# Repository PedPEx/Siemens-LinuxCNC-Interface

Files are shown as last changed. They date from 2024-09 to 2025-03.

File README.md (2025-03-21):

# Siemens Sinumerik840C control panel Interface (WIP! - UNTESTED!)
This interface board is designed to be placed on the backside of an [old type](https://mall.industry.siemens.com/mall/de/de/Catalog/Product/6FC5103-0AD03-0AA0) Siemens Sinumerik840C machine control panel in order to be used as user input in LinuxCNC. I reverse engineered a control panel of type M (CNC-Mill - 6FC5103-0AD03-0AA0) for this project. All the IOs of these control panels are accessible through the two 64pin pinheaders. You can get these machine control panels pretty cheap on ebay.

Interface:
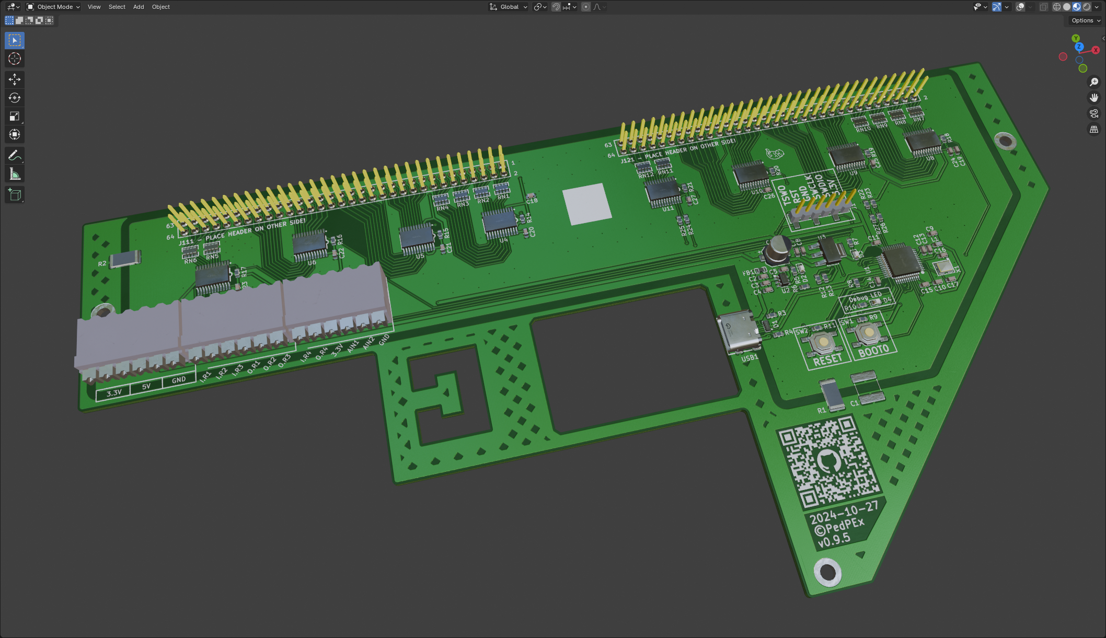
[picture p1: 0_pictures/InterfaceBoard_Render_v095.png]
v0.9.5 Blender render v0.9.5


Sinumerik840C Machine Control Panel:
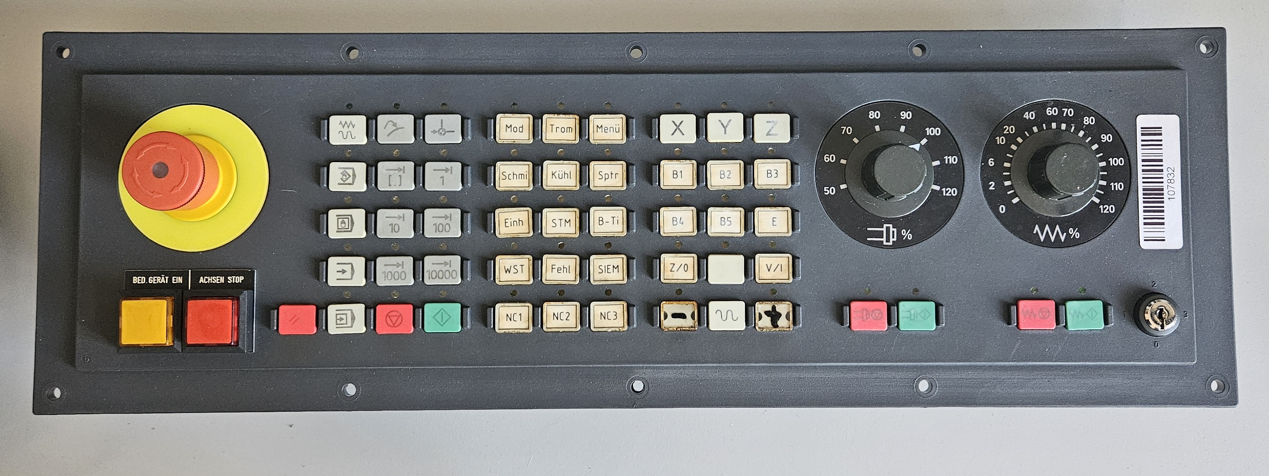
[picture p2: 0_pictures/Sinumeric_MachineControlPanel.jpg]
Sinumerik840C Machine Control Panel


## ToDo
- ✅ finished prototype PCB (v0.9.5)
- 🔲 finished prototype PCB (v0.9.6)
- ✅ firmware for STM32L151CC (technically 100% - needs cleanup and timeout detection on LinuxCNC side)
- 🔲 tested intensively with LinuxCNC
- 🔲 example config for LinuxCNC

## Powering
The board needs no seperate supply voltage and is fully powered by the USB Interface. A power distribution switch deactivates the whole interface in case of an overcurrent (set to 1.0 A).

## USB port
Plug in a USB-C cable and use the provided strain relief with the help of a 5mm cable tie. With this USB connection a virtual serial port is used to send the data to the host. More information in the [software](#usagesoftware) details.

## Terminal blocks and general IO
Most of the IO on the three terminal blocks is directly wired into the microcontroller. They can be used for analog inputs or for further expansion in general.

As terminal blocks [Weidmüller 1824460000 - LSF-SMT 3.50/06/90 3.5SN BK TU](https://catalog.weidmueller.com/catalog/Start.do?ObjectID=1824460000) were used - because i had them at hand. But any headers or screw terminals with a 3.5 mm pitch can be used here.

## Usage/Software
This interface board is meant to be used in combination with the software [LinuxCNC_ArduinoConnector](https://github.com/AlexmagToast/LinuxCNC_ArduinoConnector). It does not operate with an Arduino, but with a much more capable [STM32L151C8](https://www.st.com/en/microcontrollers-microprocessors/stm32l151cc.html). The STM32 just emulates a serial port and sends the same signals to the LinuxCNC component like the Arduino would. The L1 series of STM32 was chosen because of its bootloader

## Limitations
Do not use this board for any time critical porpuses!

## Online Preview / BOM
[Detailed schematics preview](https://kicanvas.org/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) (KiCanvas)

[Online BOM](https://htmlpreview.github.io/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)

[3D Preview](https://github.com/PedPEx/Siemens-LinuxCNC-Interface/blob/master/1_hardware/Siemens-Sinumerik840C-Maschinensteuertafel-Adaptor.stl)

## LinuxCNC config (TODO)
When finished, an example config for LinuxCNC can be found in the [correspondig folder](https://github.com/PedPEx/Siemens-LinuxCNC-Interface/tree/master/2_software_LinuxCNC).

An example of a whole machine fitted with this Interface can be found in my other project [Maho400E-LinuxCNC](https://github.com/PedPEx/Maho400E-LinuxCNC)

## *Note*
The pictures were rendered with the help of Blender and the [pcb2blender](https://github.com/30350n/pcb2blender) plugin and the HTML BOM was created with [InteractiveHtmlBom](https://github.com/openscopeproject/InteractiveHtmlBom).

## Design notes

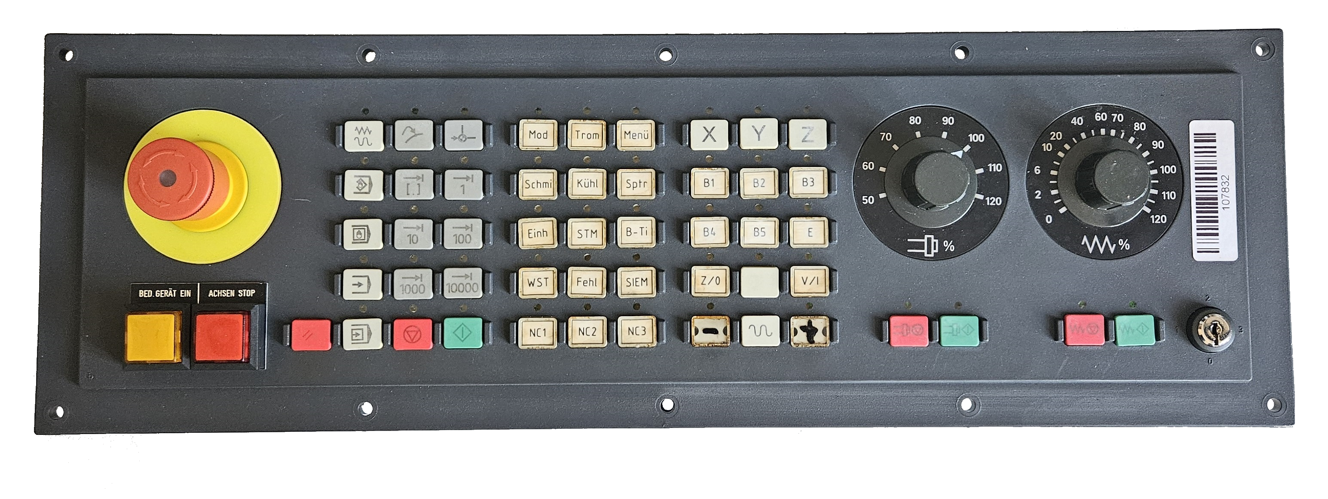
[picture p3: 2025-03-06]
0_pictures/Sinumeric_MachineControlPanel.png

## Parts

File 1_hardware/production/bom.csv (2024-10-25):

Designator | Footprint | Quantity | Value | LCSC Part #
C1 | 2220 | 1 | 0.1u | C5290327
C10, C11, C13, C14, C15, C19, C20, C21, C22, C24, C25, C26, C27 | 0603 | 13 | 100n
C12, C2 | 0603 | 2 | 1u
C16, C17 | 0603 | 2 | 8p
C18, C23, C9 | 0603 | 3 | 4u7
C3, C8 | 0603 | 2 | 10u
C4, C5, C7 | 0603 | 3 | 0.1u
C6 | CP_Elec_5x5.8 | 1 | 100u | C336771
D1 | USON-10_L2.5-W1.0-P0.50-BL | 1 | TPD4E05U06DQAR_C138714 | C138714
D2, D3, D4 | 0603 | 3 | LED
FB1 | L0603 | 1 | 100R@100MHz | C107332
J1 | HDR-SMD_6P-P2.54-V-M-LS4.8_R2 | 1 | ProgHeader | C2883763
J111, J121 | SAMTEC_SSW-132-24-L-D | 2 | SSW-132-24-L-D
J2 | 1824460000 - LSF-SMT 3.500690 3.5SN BK TU | 1 | Power
J3 | 1824460000 - LSF-SMT 3.500690 3.5SN BK TU | 1 | Buttons
J4 | 1824460000 - LSF-SMT 3.500690 3.5SN BK TU | 1 | Reserve2
L1 | 0603 | 1 | 27nH | C12100
R1, R2 | 2512 | 2 | 100k | C25717
R10, R7 | 0603 | 2 | 470
R11, R14, R15, R16, R17, R18, R19, R20, R21, R9 | 0603 | 10 | 10k
R12, R13, R22, R23, R8 | 0603 | 5 | 1k5
R24, R25, R26, R27 | 0603 | 4 | 0
R3, R4 | 0603 | 2 | 5k1
R5 | 0603 | 1 | 680
R6 | 0603 | 1 | 25k
RN1, RN10, RN11, RN12, RN2, RN3, RN4, RN5, RN6, RN7, RN8, RN9 | RES-ARRAY-SMD_0603-8P-L3.2-W1.6-BL | 12 | 4x680R | C12035
SW1, SW2 | SW-SMD_4P-L5.1-W5.1-P3.70-LS6.5-TL-2 | 2 | TS-1187A-B-A-B | C318884
TP1 | TestPoint_Pad_D1.0mm | 1 | GND
TP2 | TestPoint_Pad_D1.0mm | 1 | JTDI
TP3 | TestPoint_Pad_D1.0mm | 1 | JTMS-SWDIO
TP4 | TestPoint_Pad_D1.0mm | 1 | JTCK-SWCLK
TP5 | TestPoint_Pad_D1.0mm | 1 | JTDO-TraceSWO
TP6 | TestPoint_Pad_D1.0mm | 1 | RESET
U1 | LQFP-48_L7.0-W7.0-P0.50-LS9.0-BL | 1 | STM32L151C8T6 | C9861
U10, U11, U4, U5, U6, U7, U8, U9 | TSSOP-24_L7.8-W4.4-P0.65-LS6.4-BL | 8 | PCA9555PW,118 | C128392
U2 | SOT-23-6_L2.9-W1.6-P0.95-LS2.8-BL | 1 | AP22652AW6-7 | C5329413
U3 | SOT-223-4_L6.5-W3.5-P2.30-LS7.0-BR | 1 | LD1117S33CTR | C35879
USB1 | USB-C-SMD_KH-TYPE-C-16P | 1 | KH-TYPE-C-16P | C709357
X1 | CRYSTAL-SMD_4P-L3.2-W2.5-BL_SIT8008BI | 1 | 16MHz | C498200

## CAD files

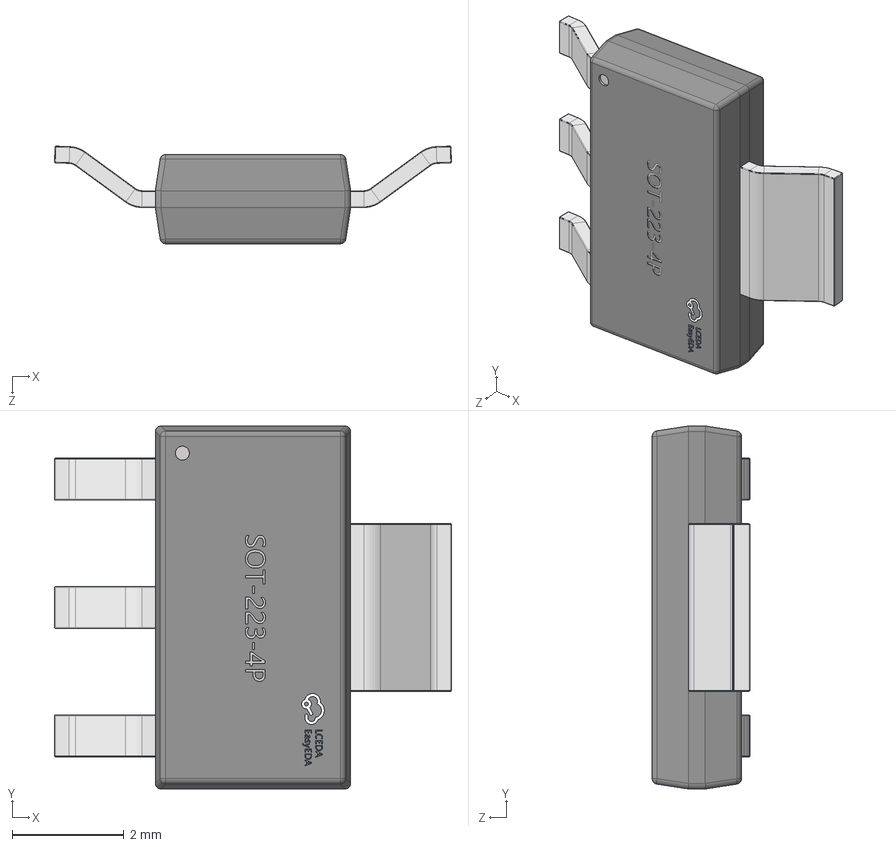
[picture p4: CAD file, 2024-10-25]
1_hardware/project_library/project_library_3D/SOT-223-4P_L6.5-W3.5-H1.6-LS7.0-P2.30.step
7.11 x 6.50 x 1.75 mm

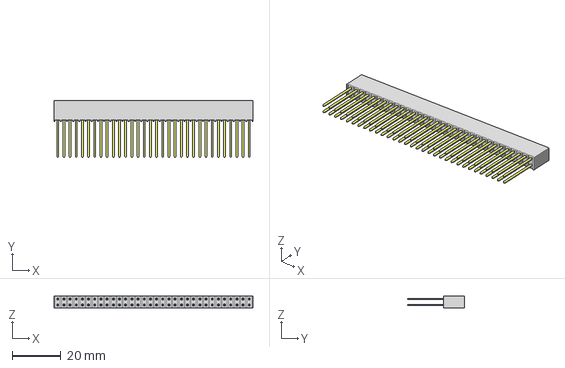
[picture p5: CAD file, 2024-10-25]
1_hardware/project_library/project_library_3D/SSW-132-24-L-D.step
81.8 x 23.3 x 4.95 mm
T1SSW-132-24-L-D
P2SSW-132-24-L-D

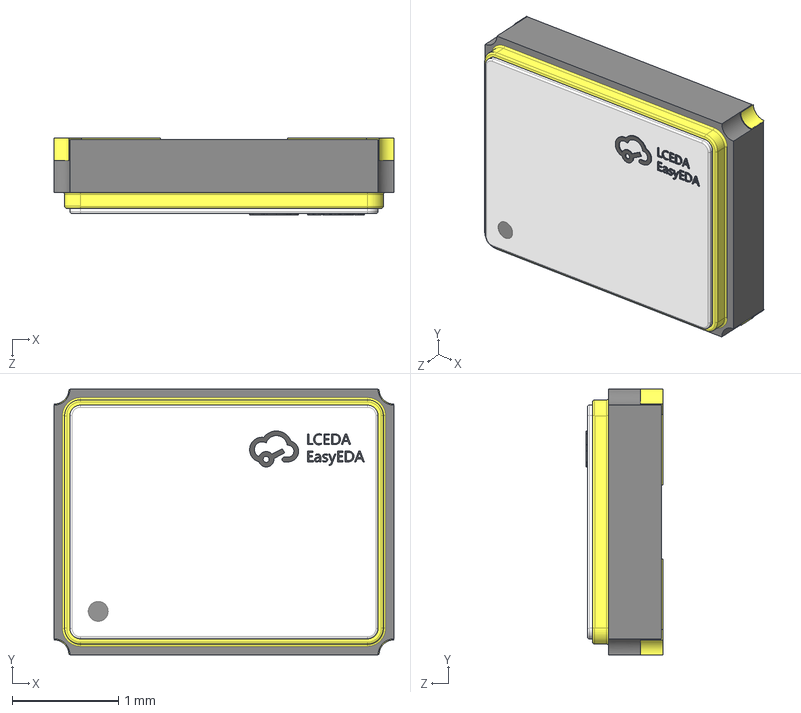
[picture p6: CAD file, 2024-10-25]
1_hardware/project_library/project_library_3D/CRYSTAL-SMD_4P-L3.2-W2.5-BL_SIT8008BI.step
3.20 x 2.50 x 0.72 mm

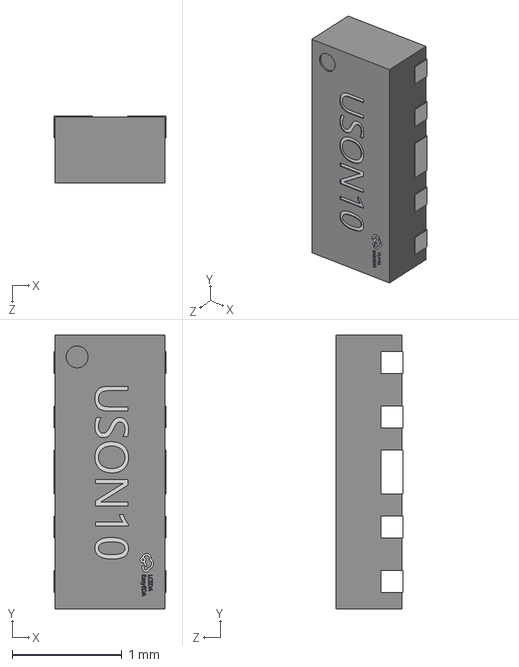
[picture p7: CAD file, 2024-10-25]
1_hardware/project_library/project_library_3D/USON-10_L2.5-W1.0-H0.6-P0.50.step
1.02 x 2.50 x 0.611 mm

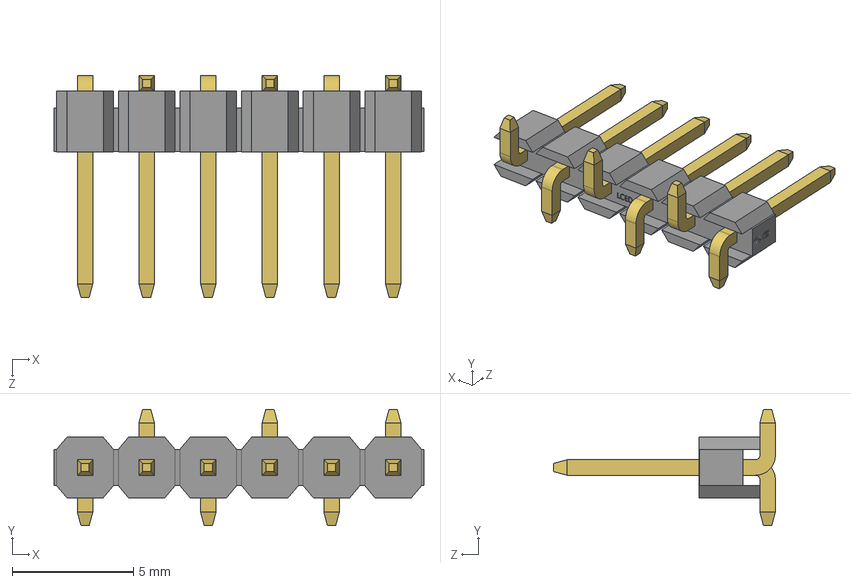
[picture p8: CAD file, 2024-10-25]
1_hardware/project_library/project_library_3D/HDR-SMD_6P-P2.54-V-M-LS4.8_R2.step
15.3 x 4.80 x 9.14 mm

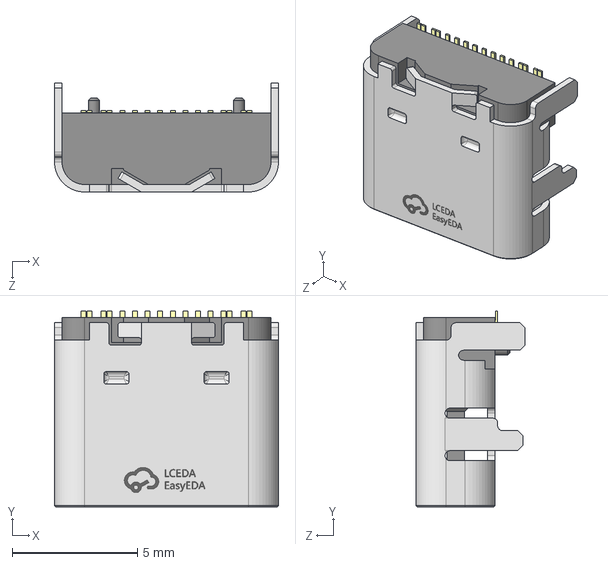
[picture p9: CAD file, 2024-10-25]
1_hardware/project_library/project_library_3D/USB-C-SMD_KH-TYPE-C-16P.step
8.94 x 7.81 x 4.35 mm

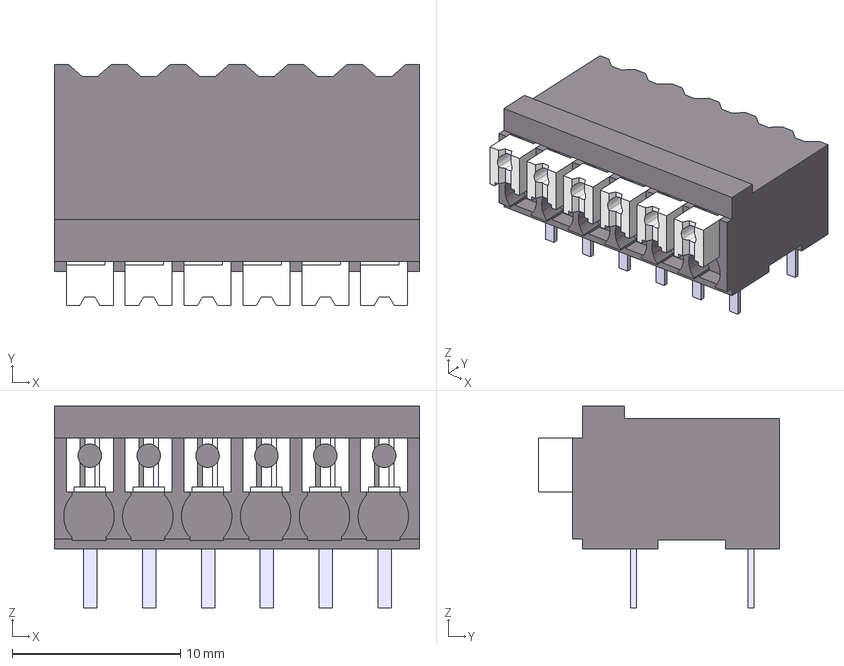
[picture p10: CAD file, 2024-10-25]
1_hardware/project_library/project_library_3D/1824460000.stp
21.7 x 14.3 x 12.0 mm

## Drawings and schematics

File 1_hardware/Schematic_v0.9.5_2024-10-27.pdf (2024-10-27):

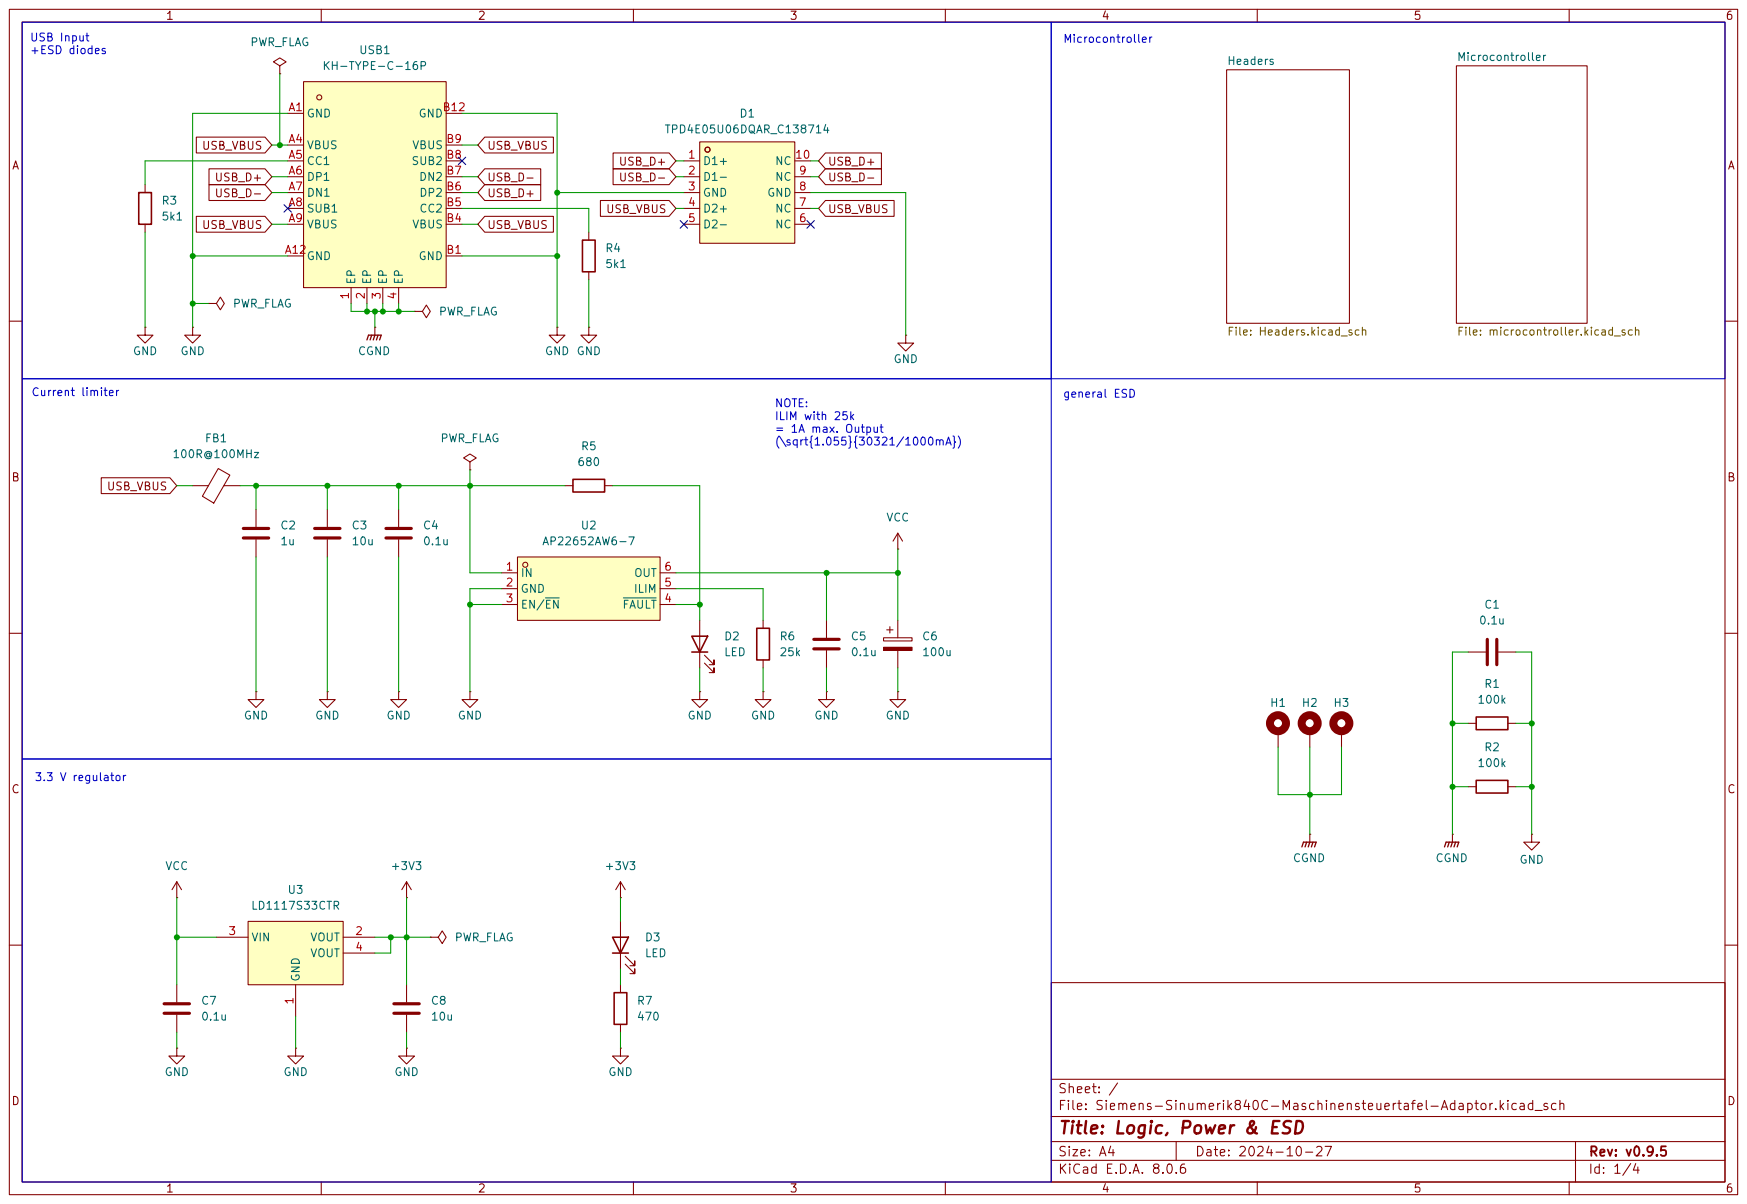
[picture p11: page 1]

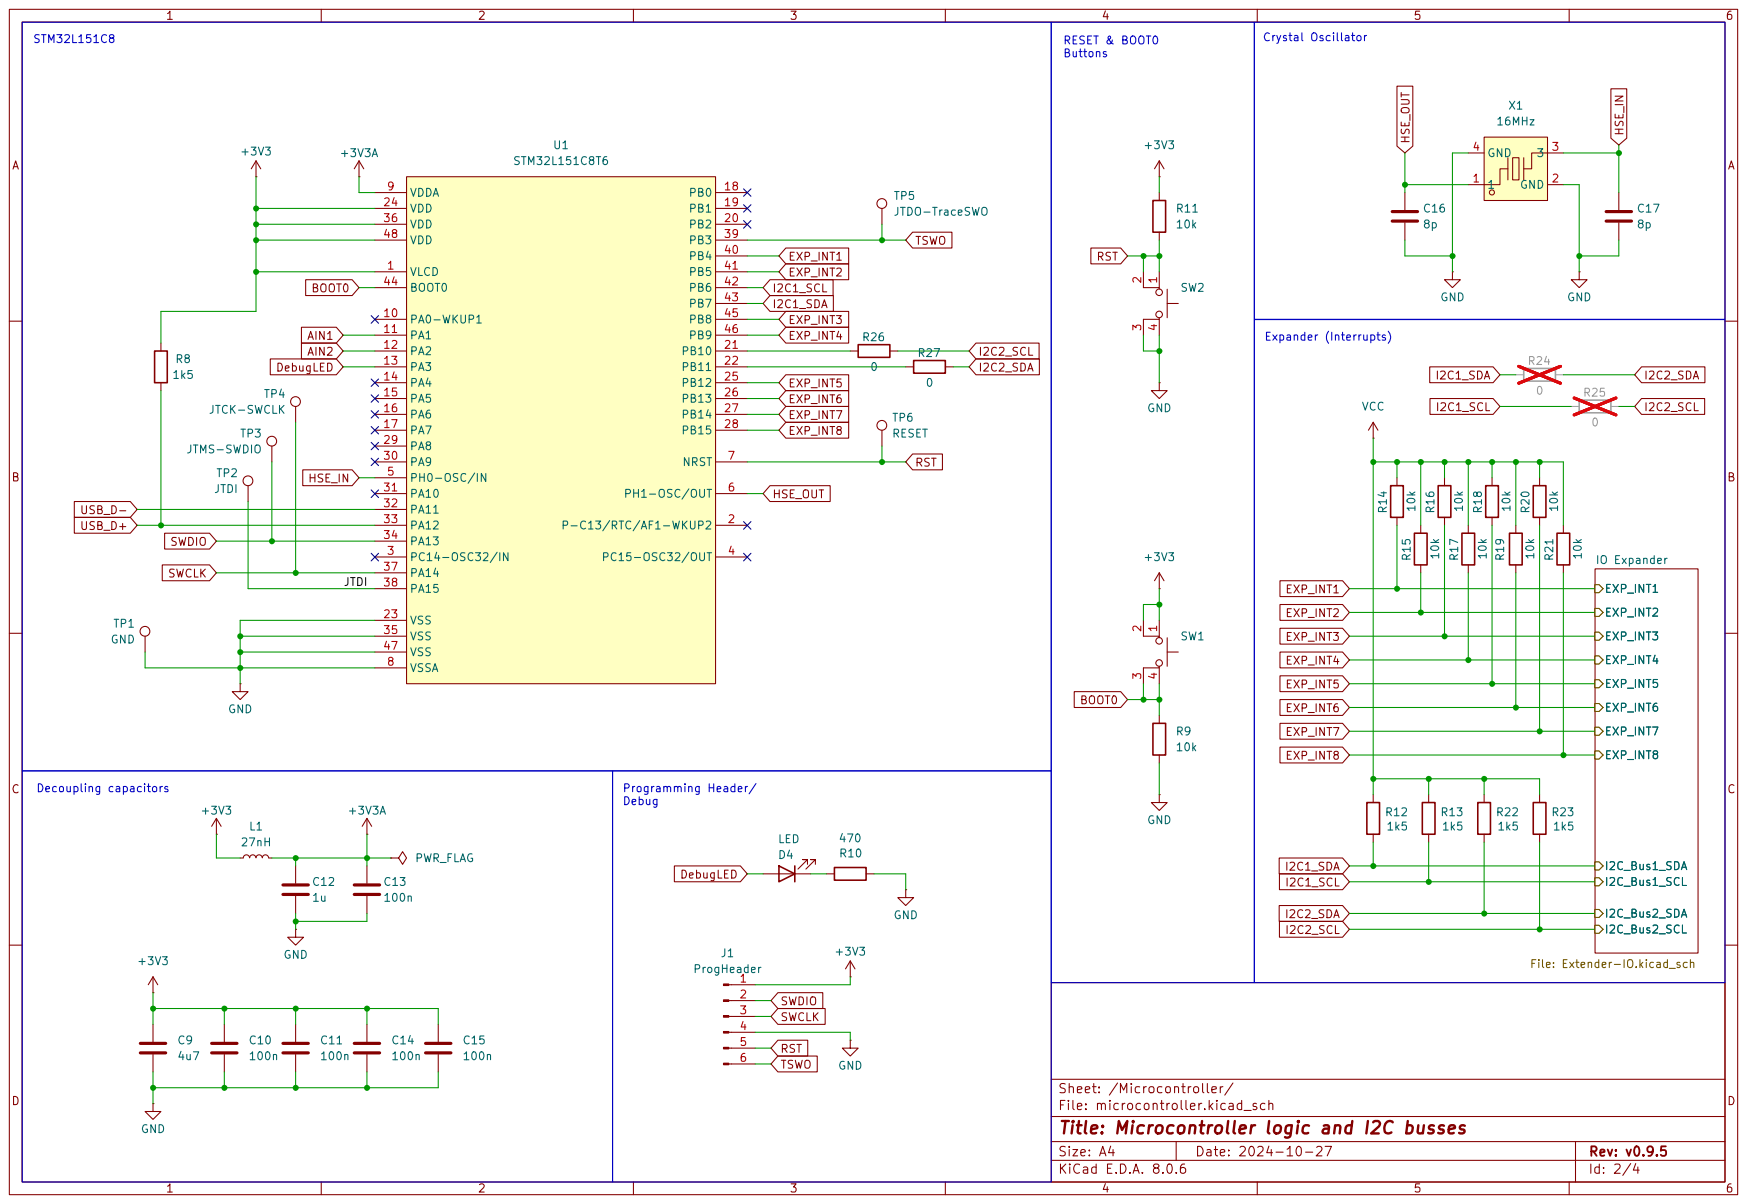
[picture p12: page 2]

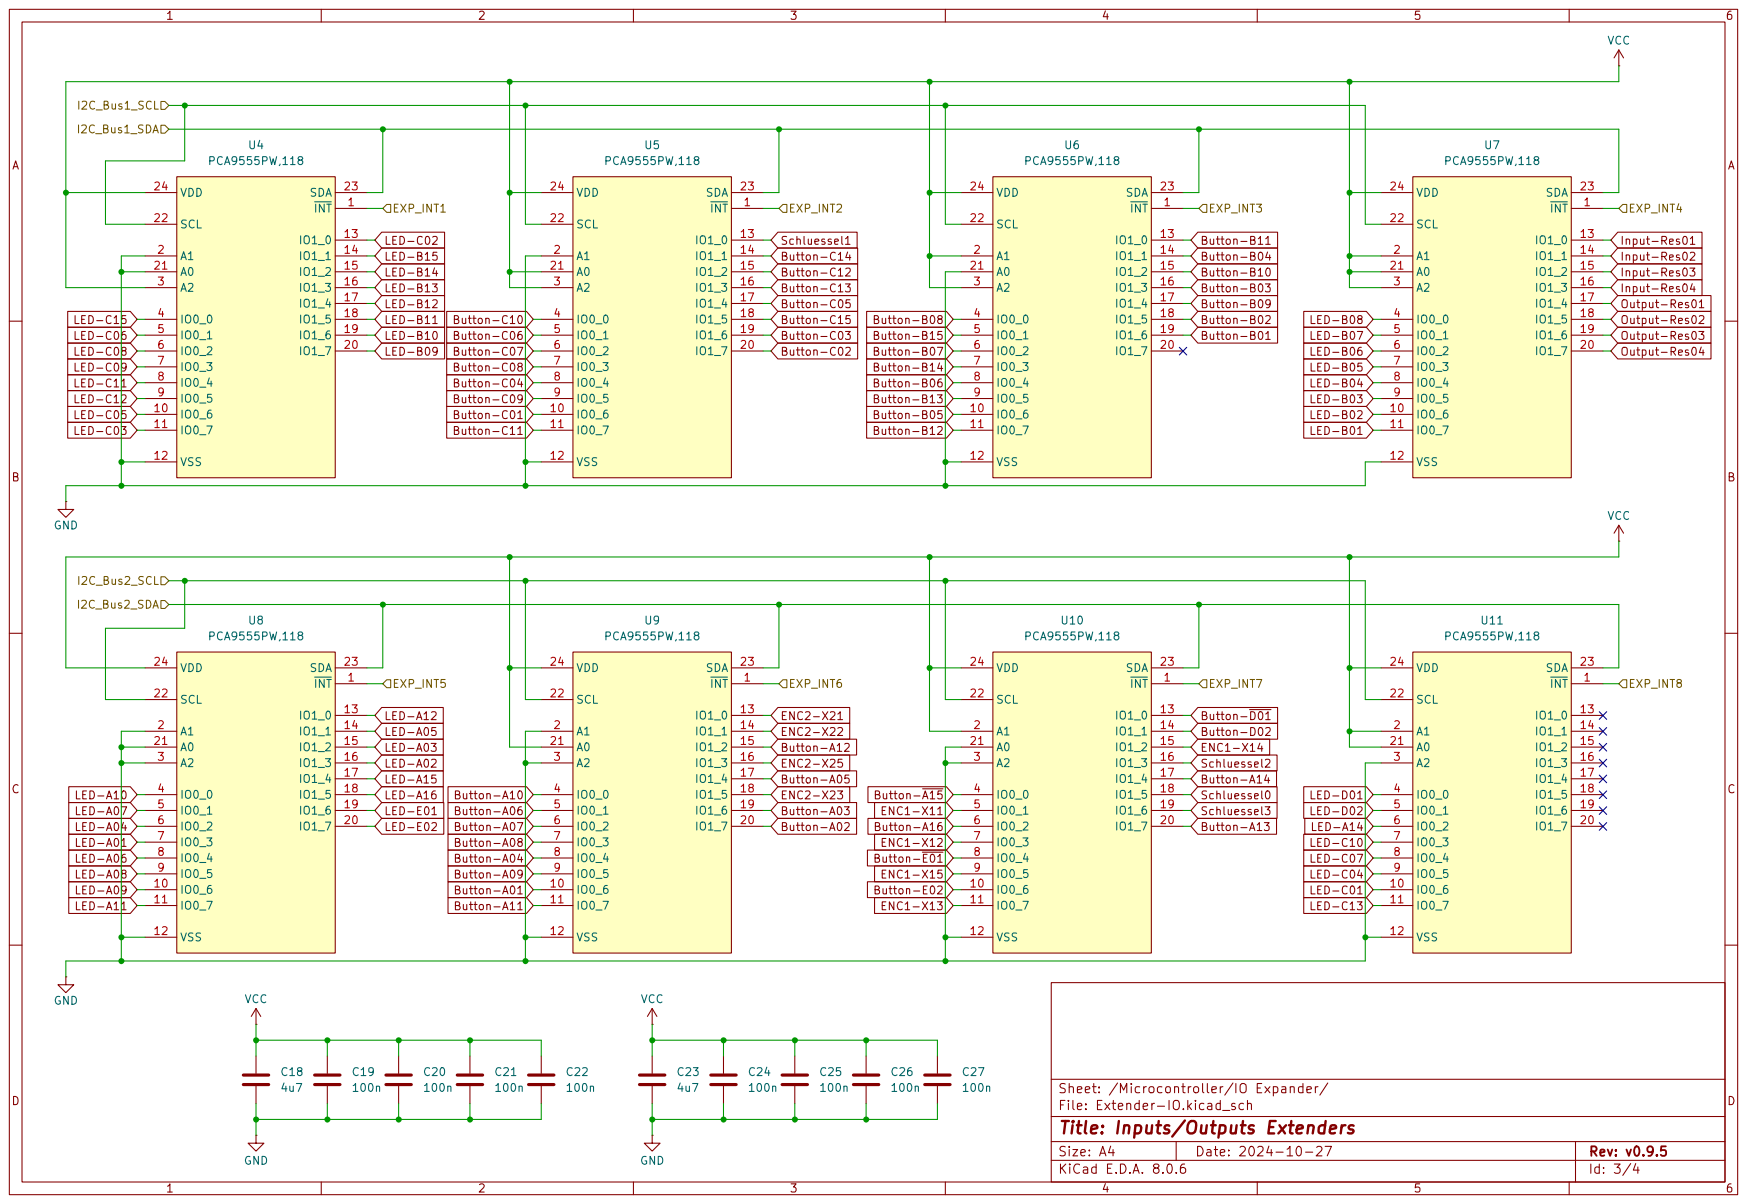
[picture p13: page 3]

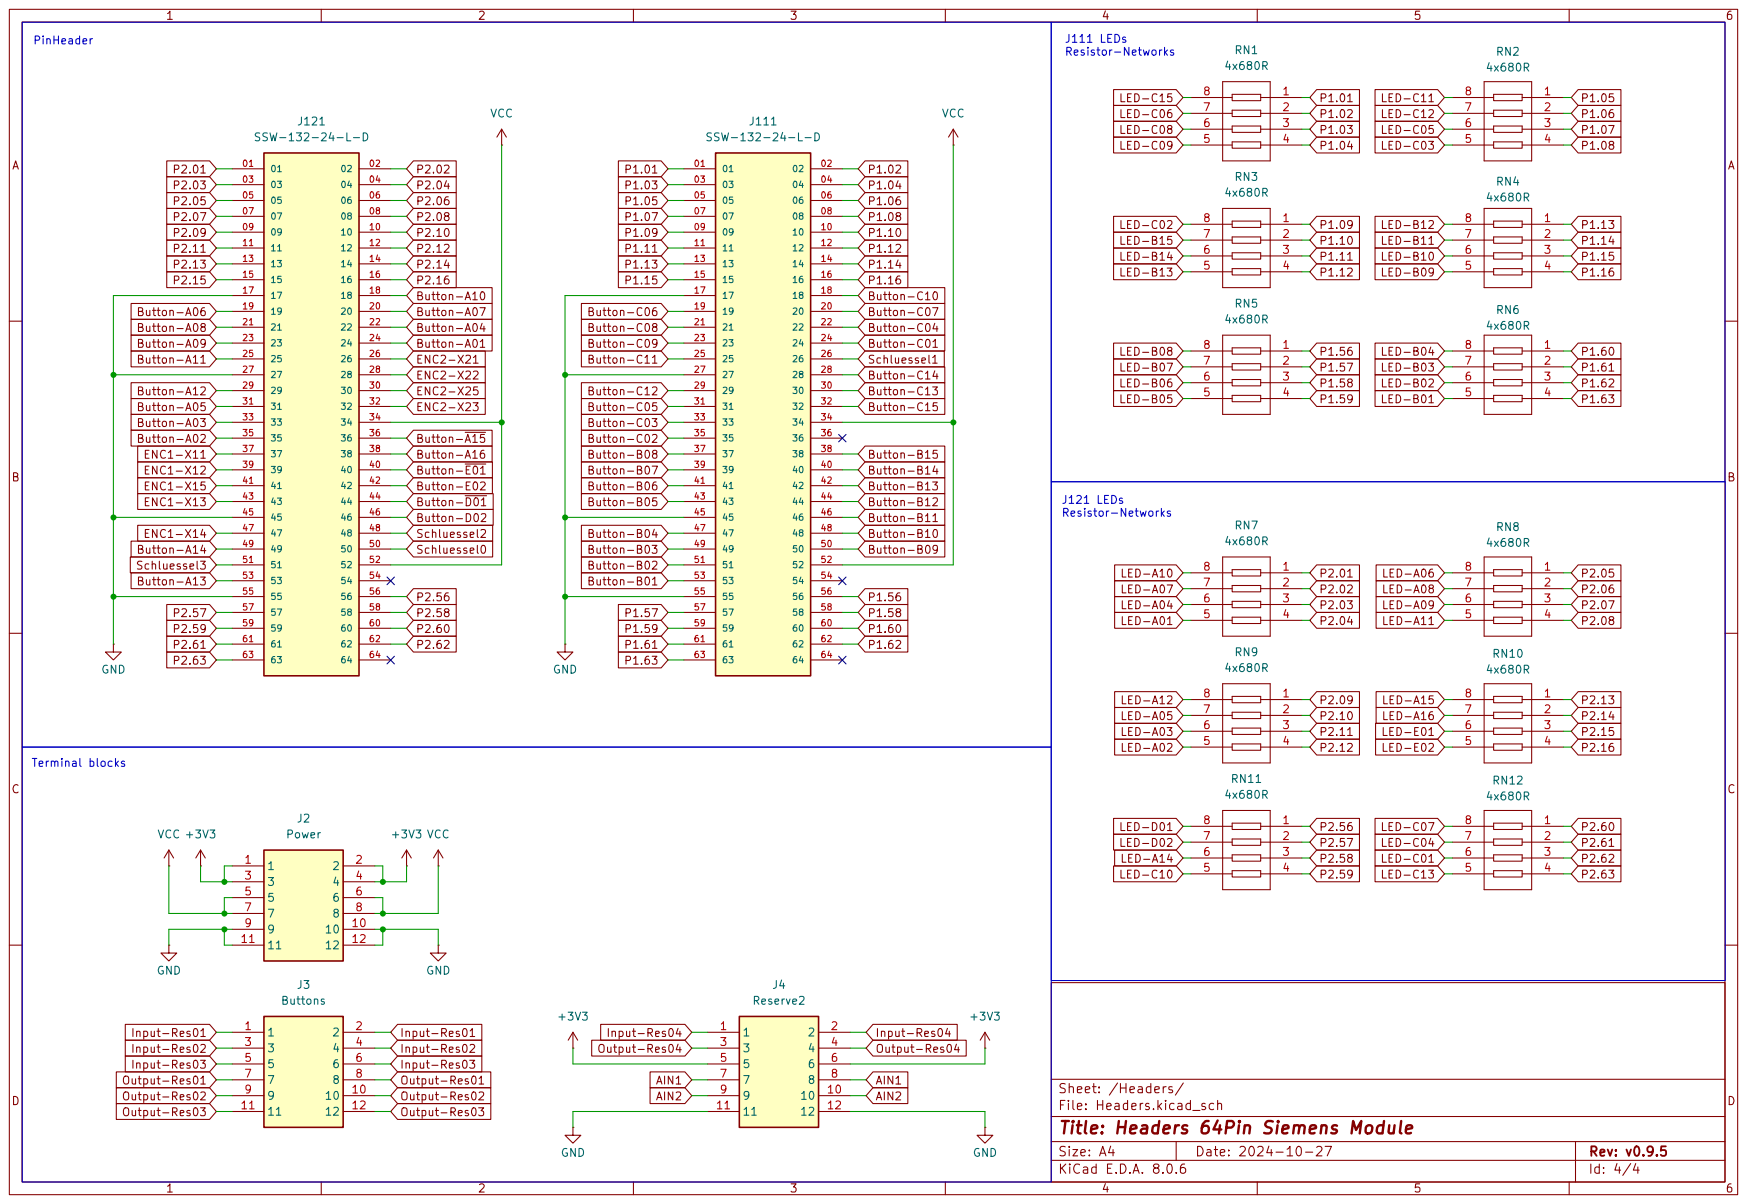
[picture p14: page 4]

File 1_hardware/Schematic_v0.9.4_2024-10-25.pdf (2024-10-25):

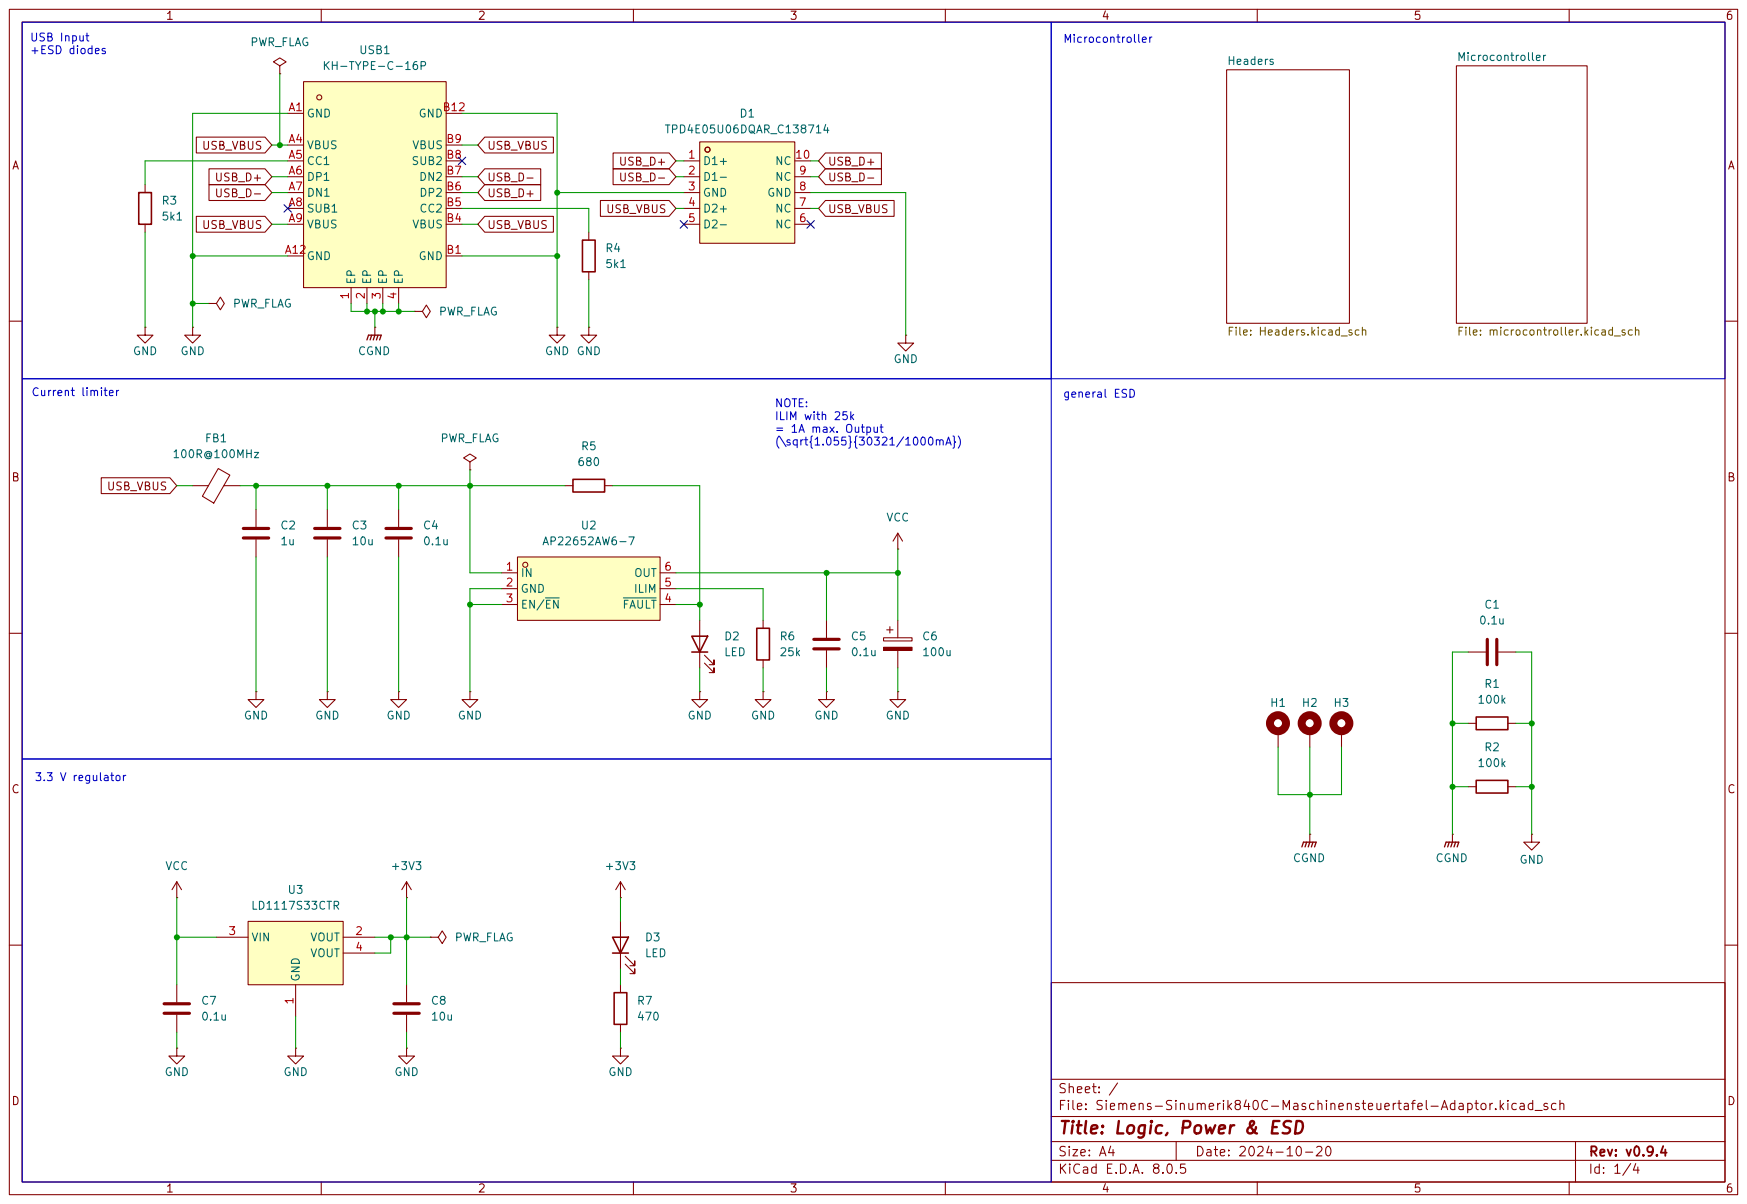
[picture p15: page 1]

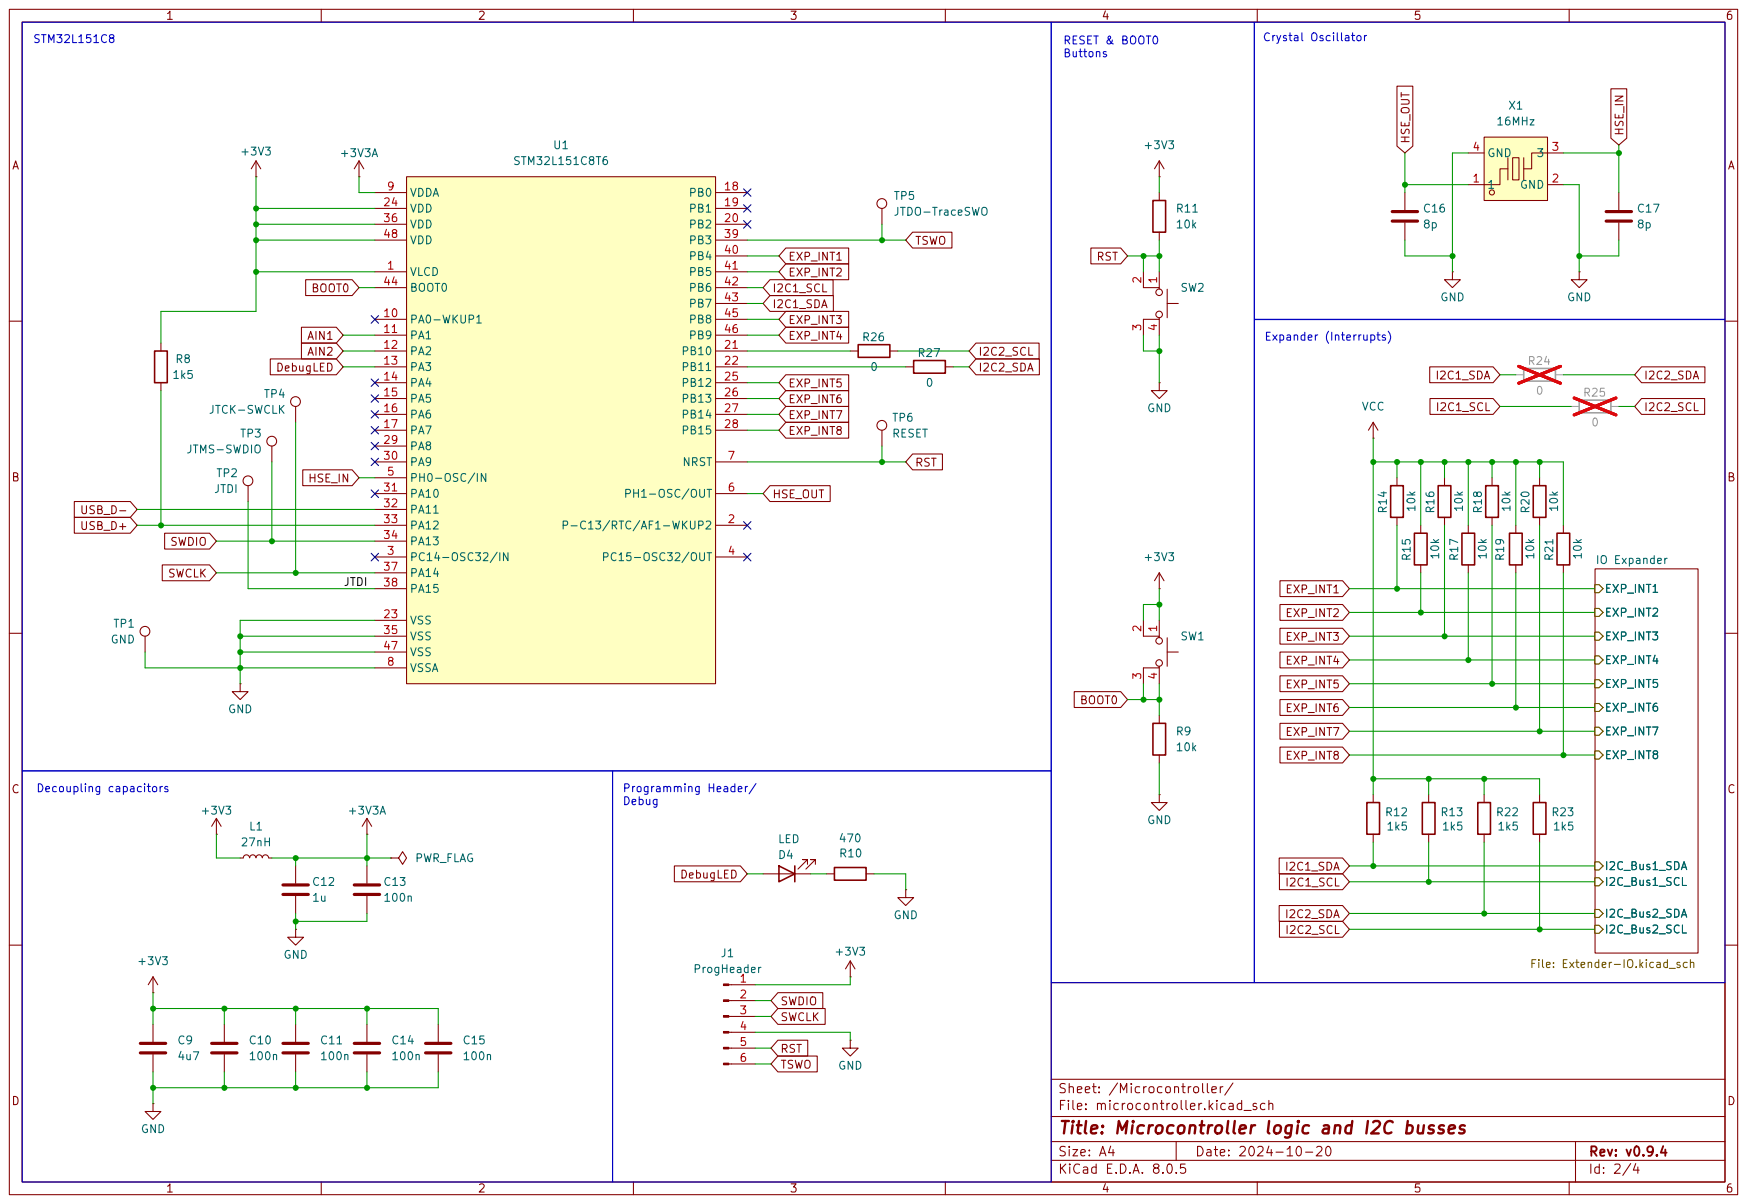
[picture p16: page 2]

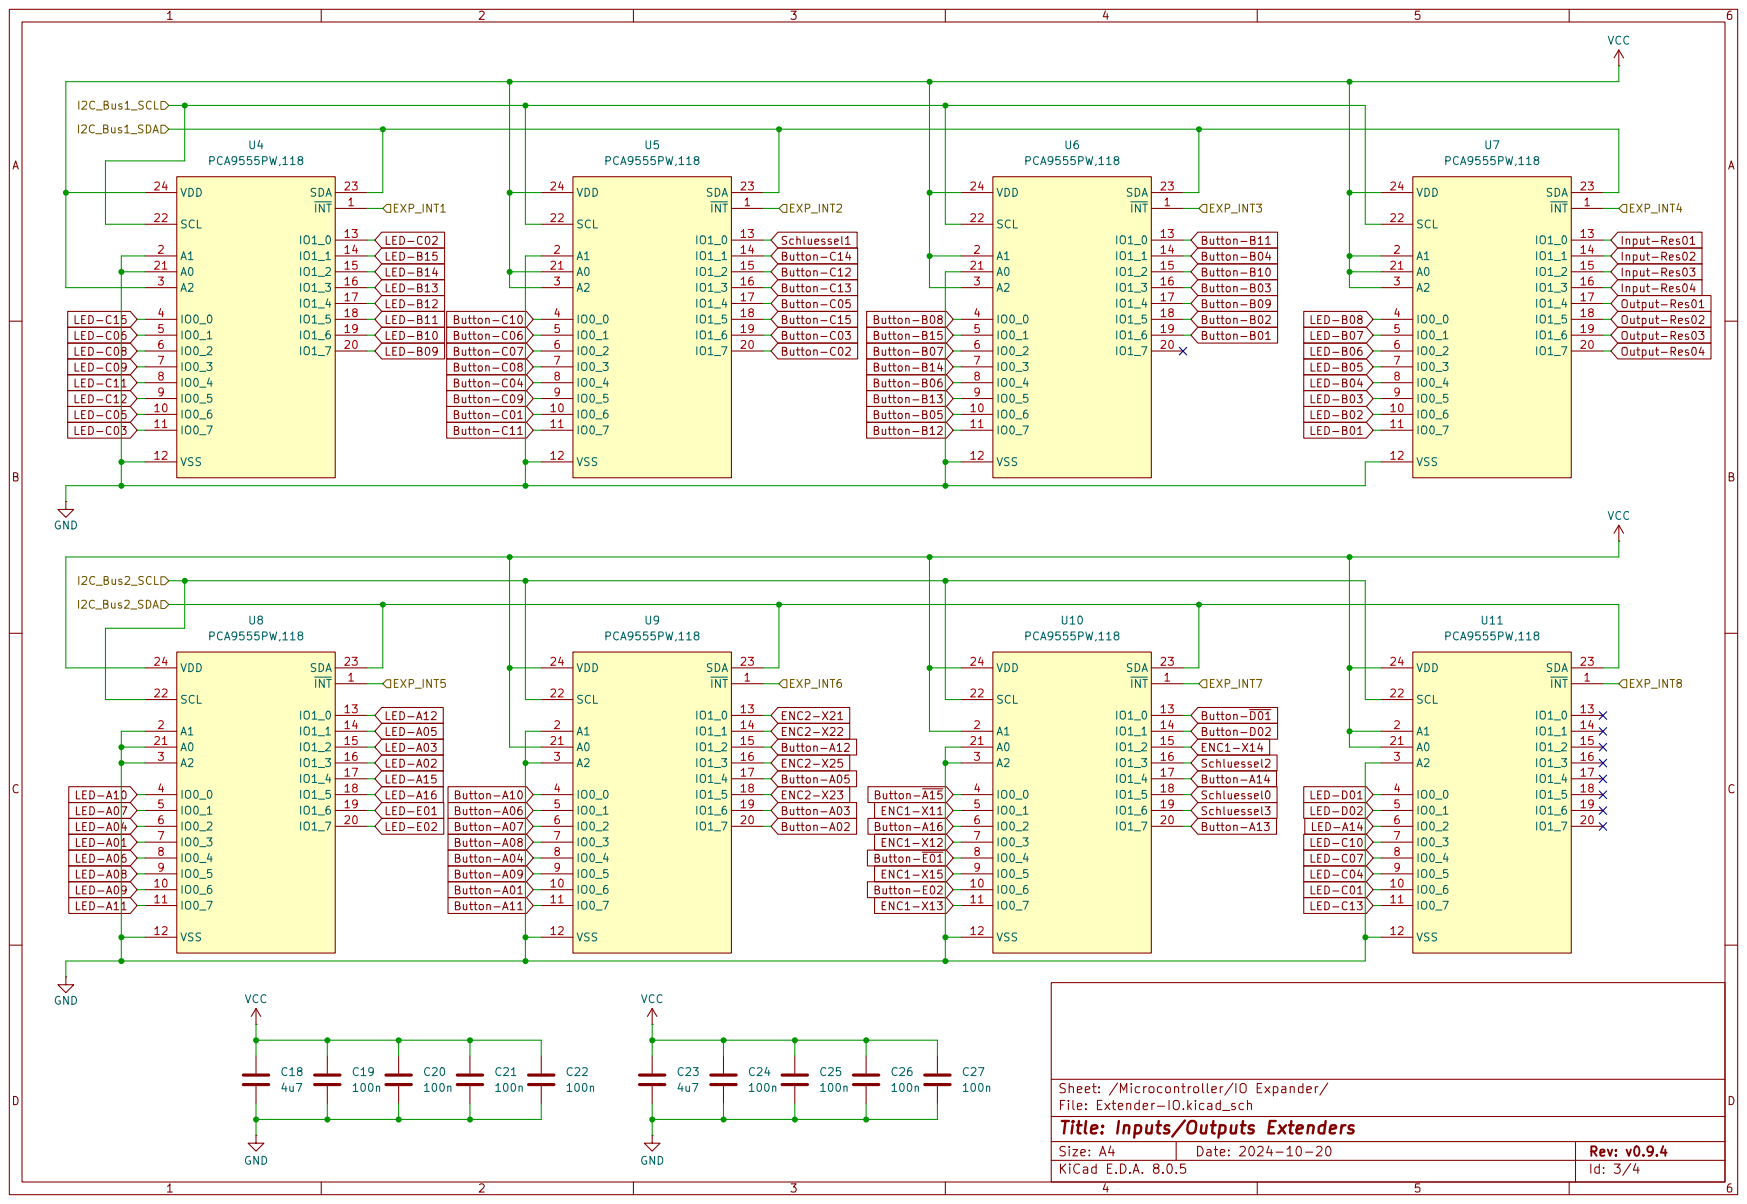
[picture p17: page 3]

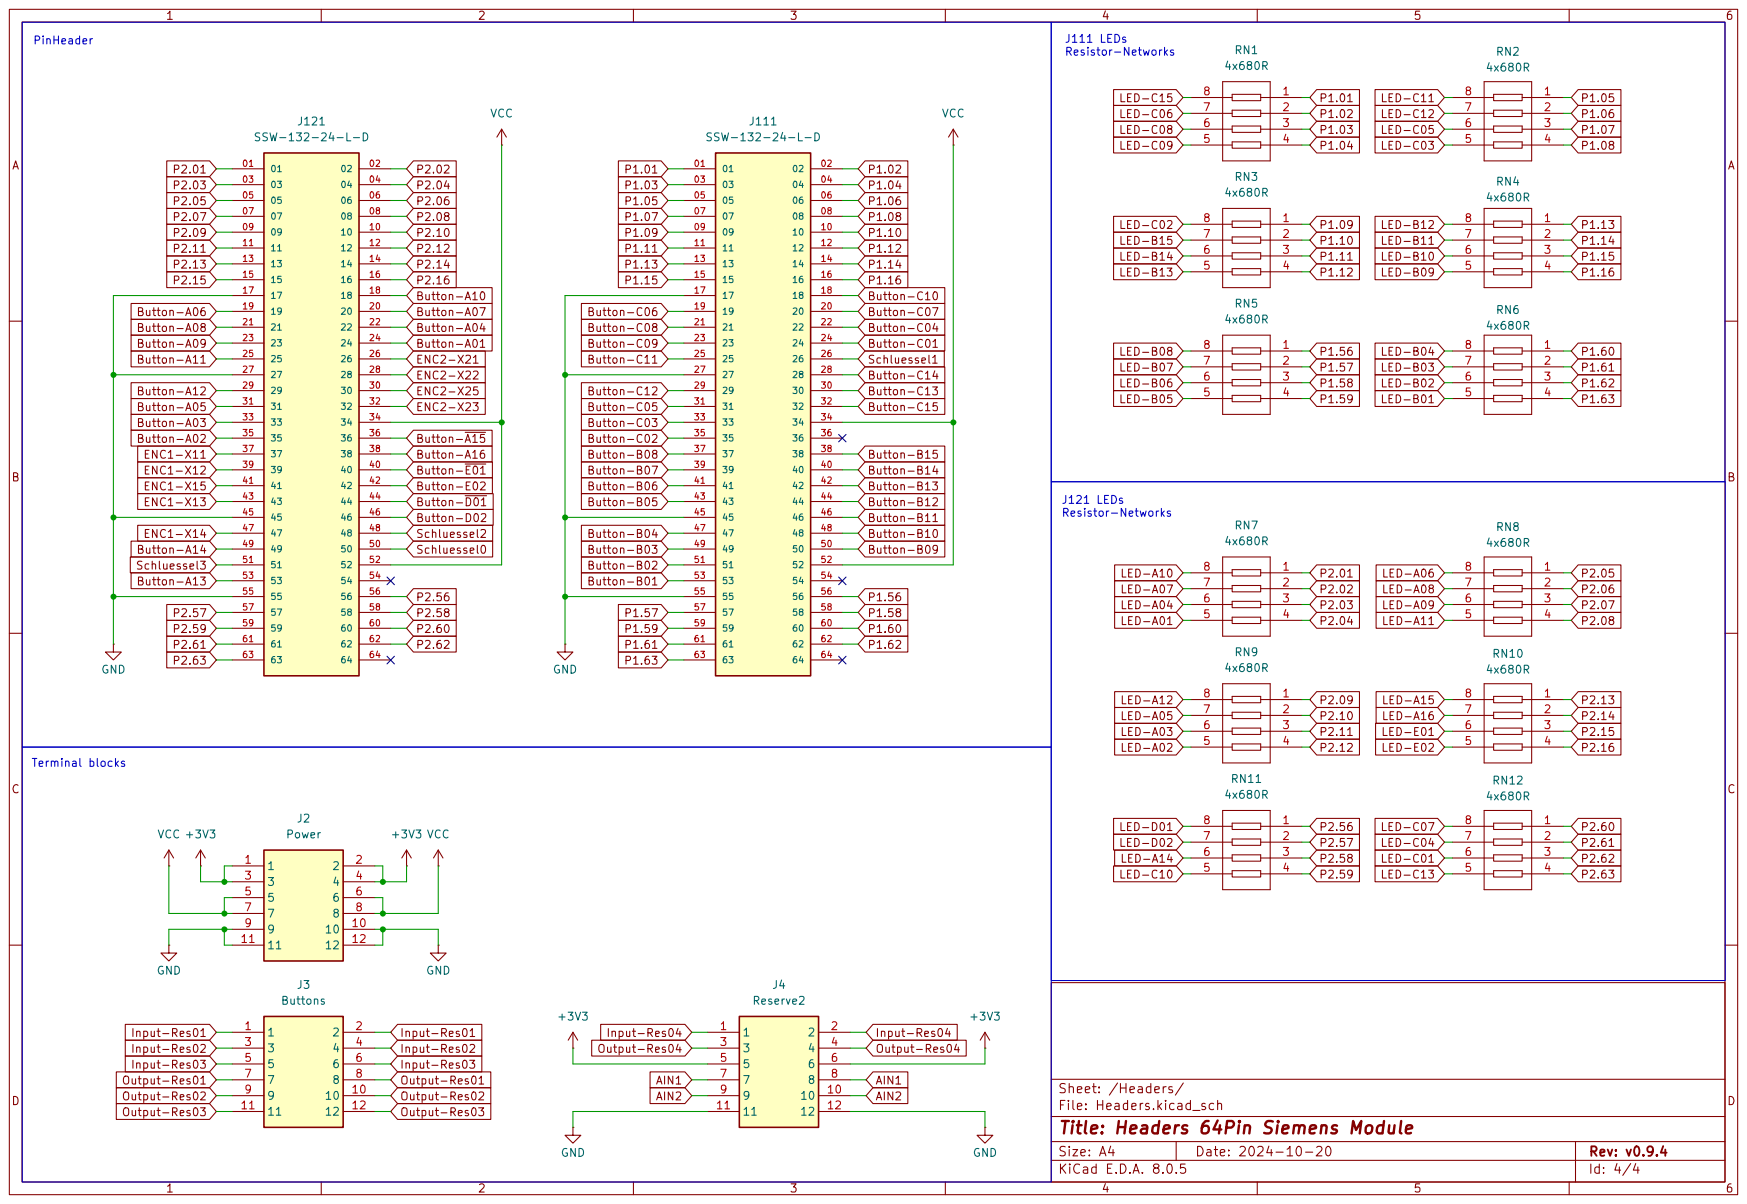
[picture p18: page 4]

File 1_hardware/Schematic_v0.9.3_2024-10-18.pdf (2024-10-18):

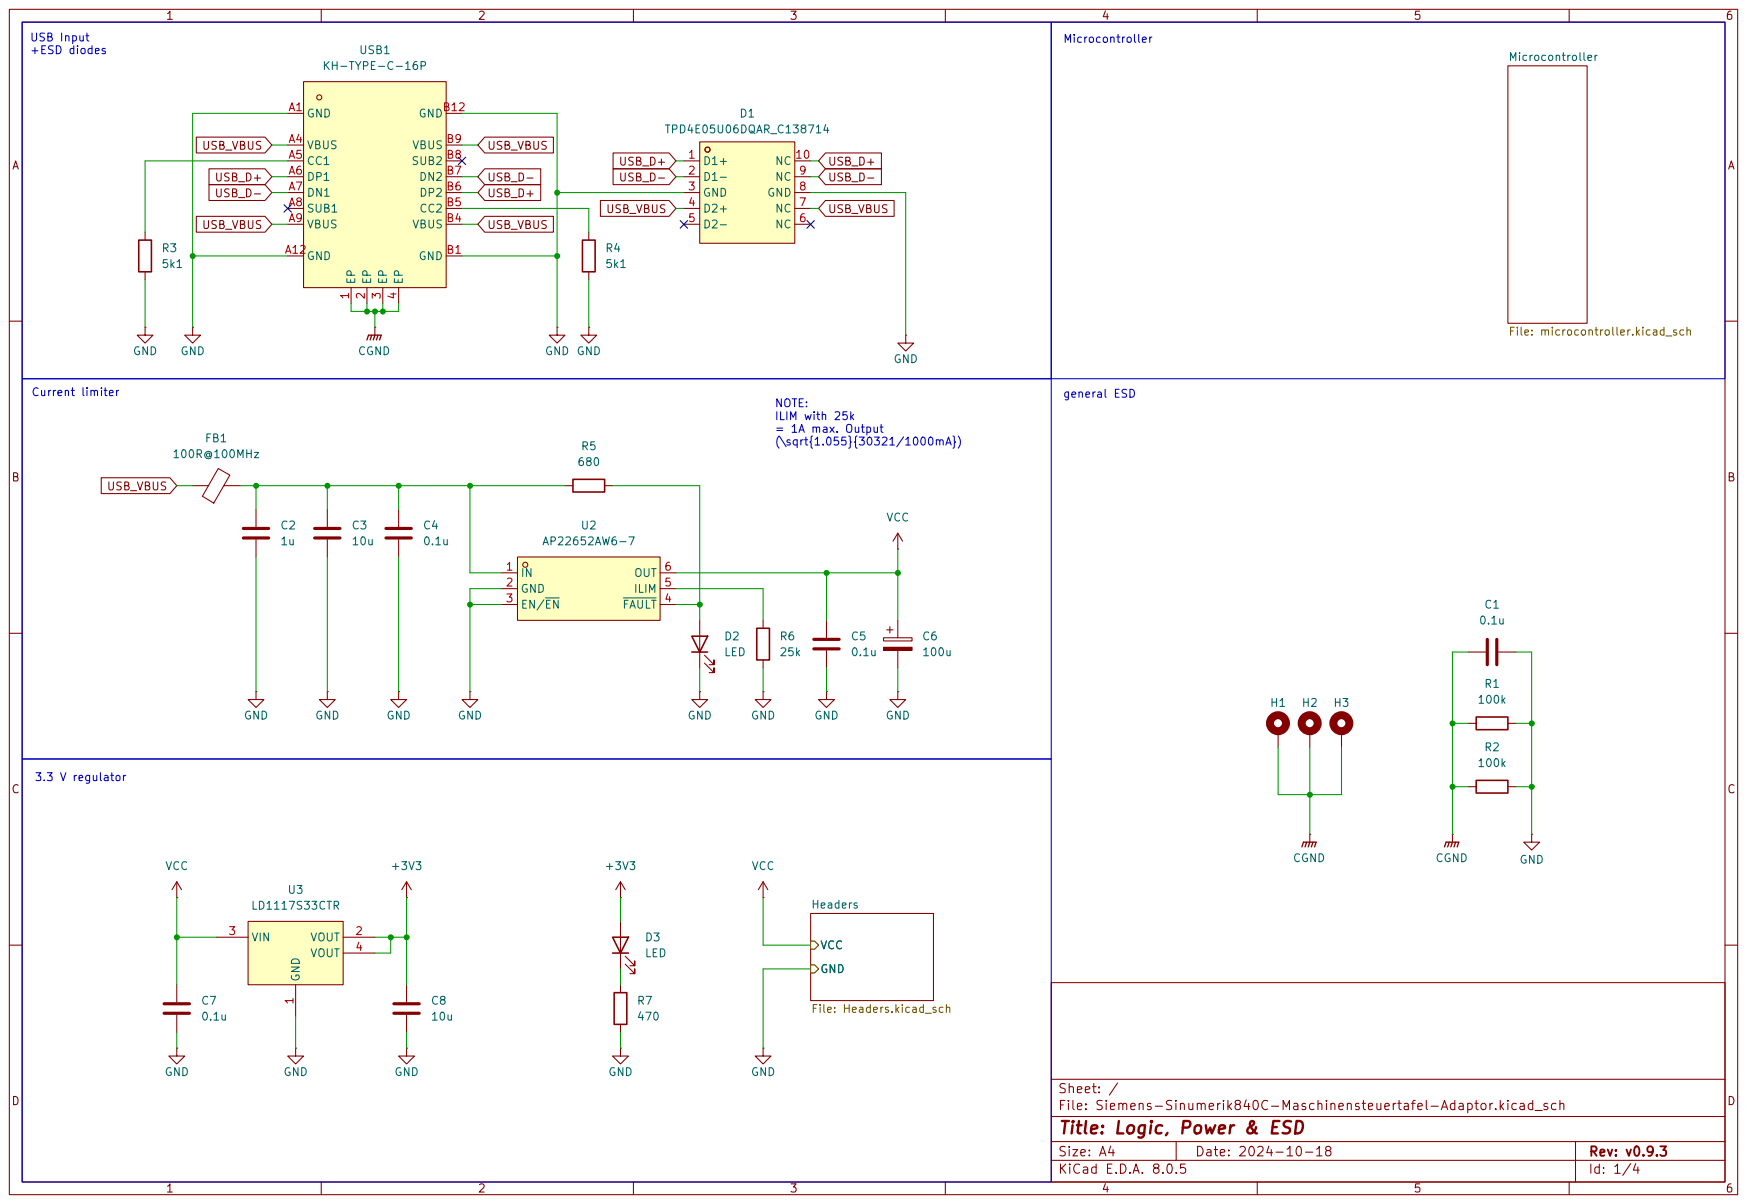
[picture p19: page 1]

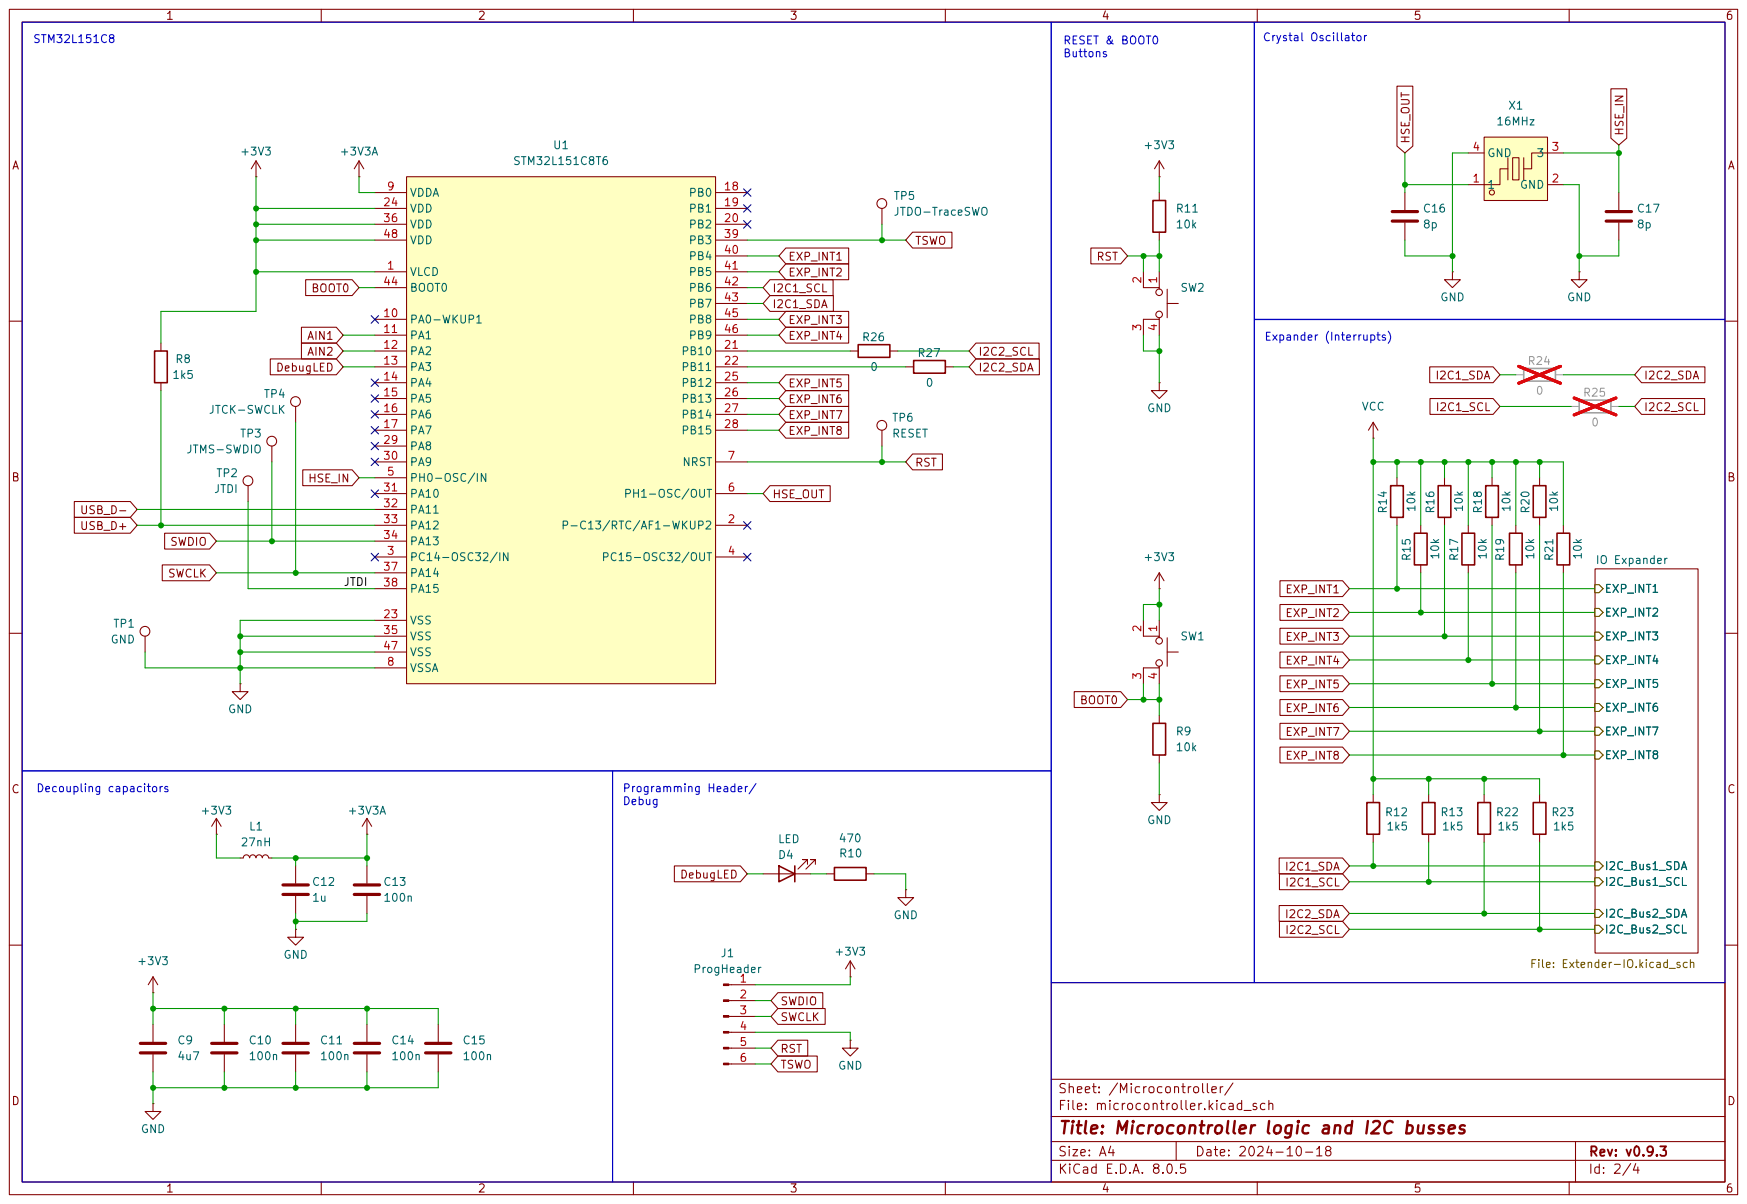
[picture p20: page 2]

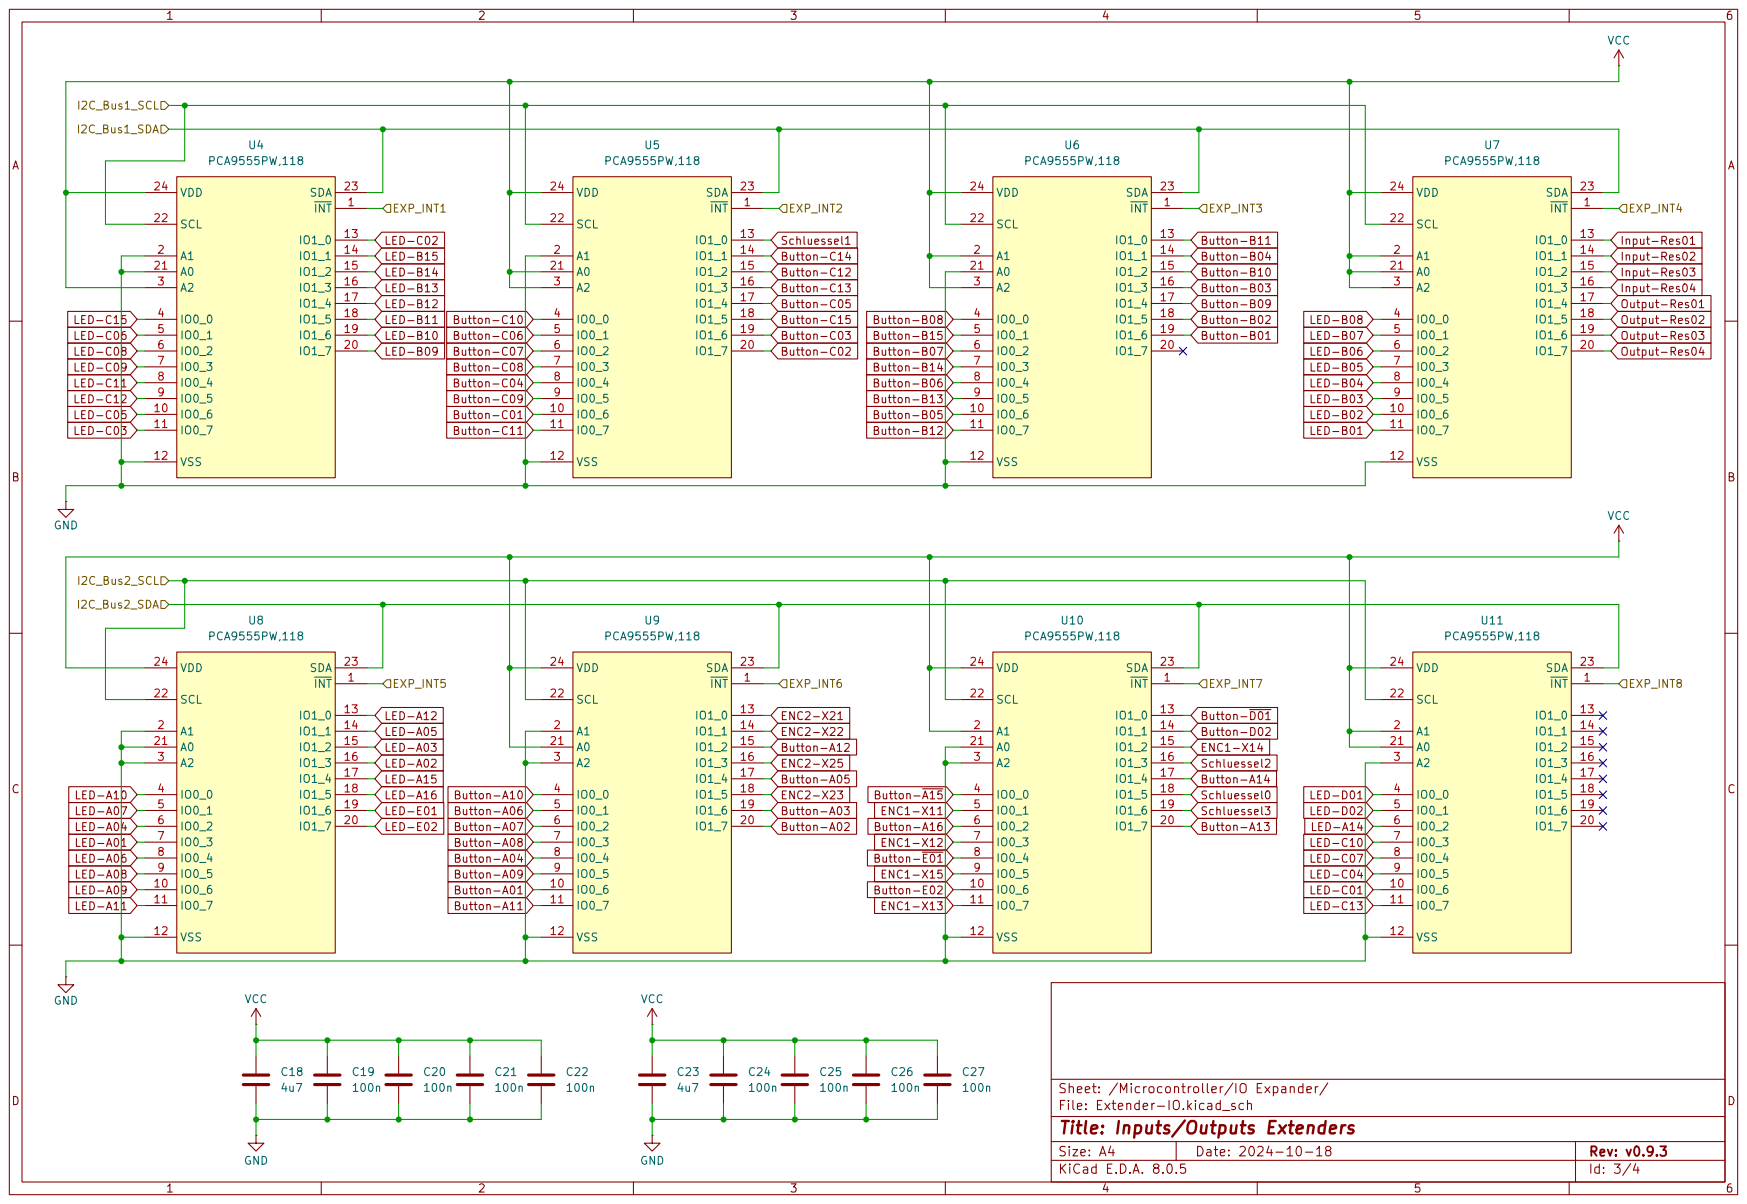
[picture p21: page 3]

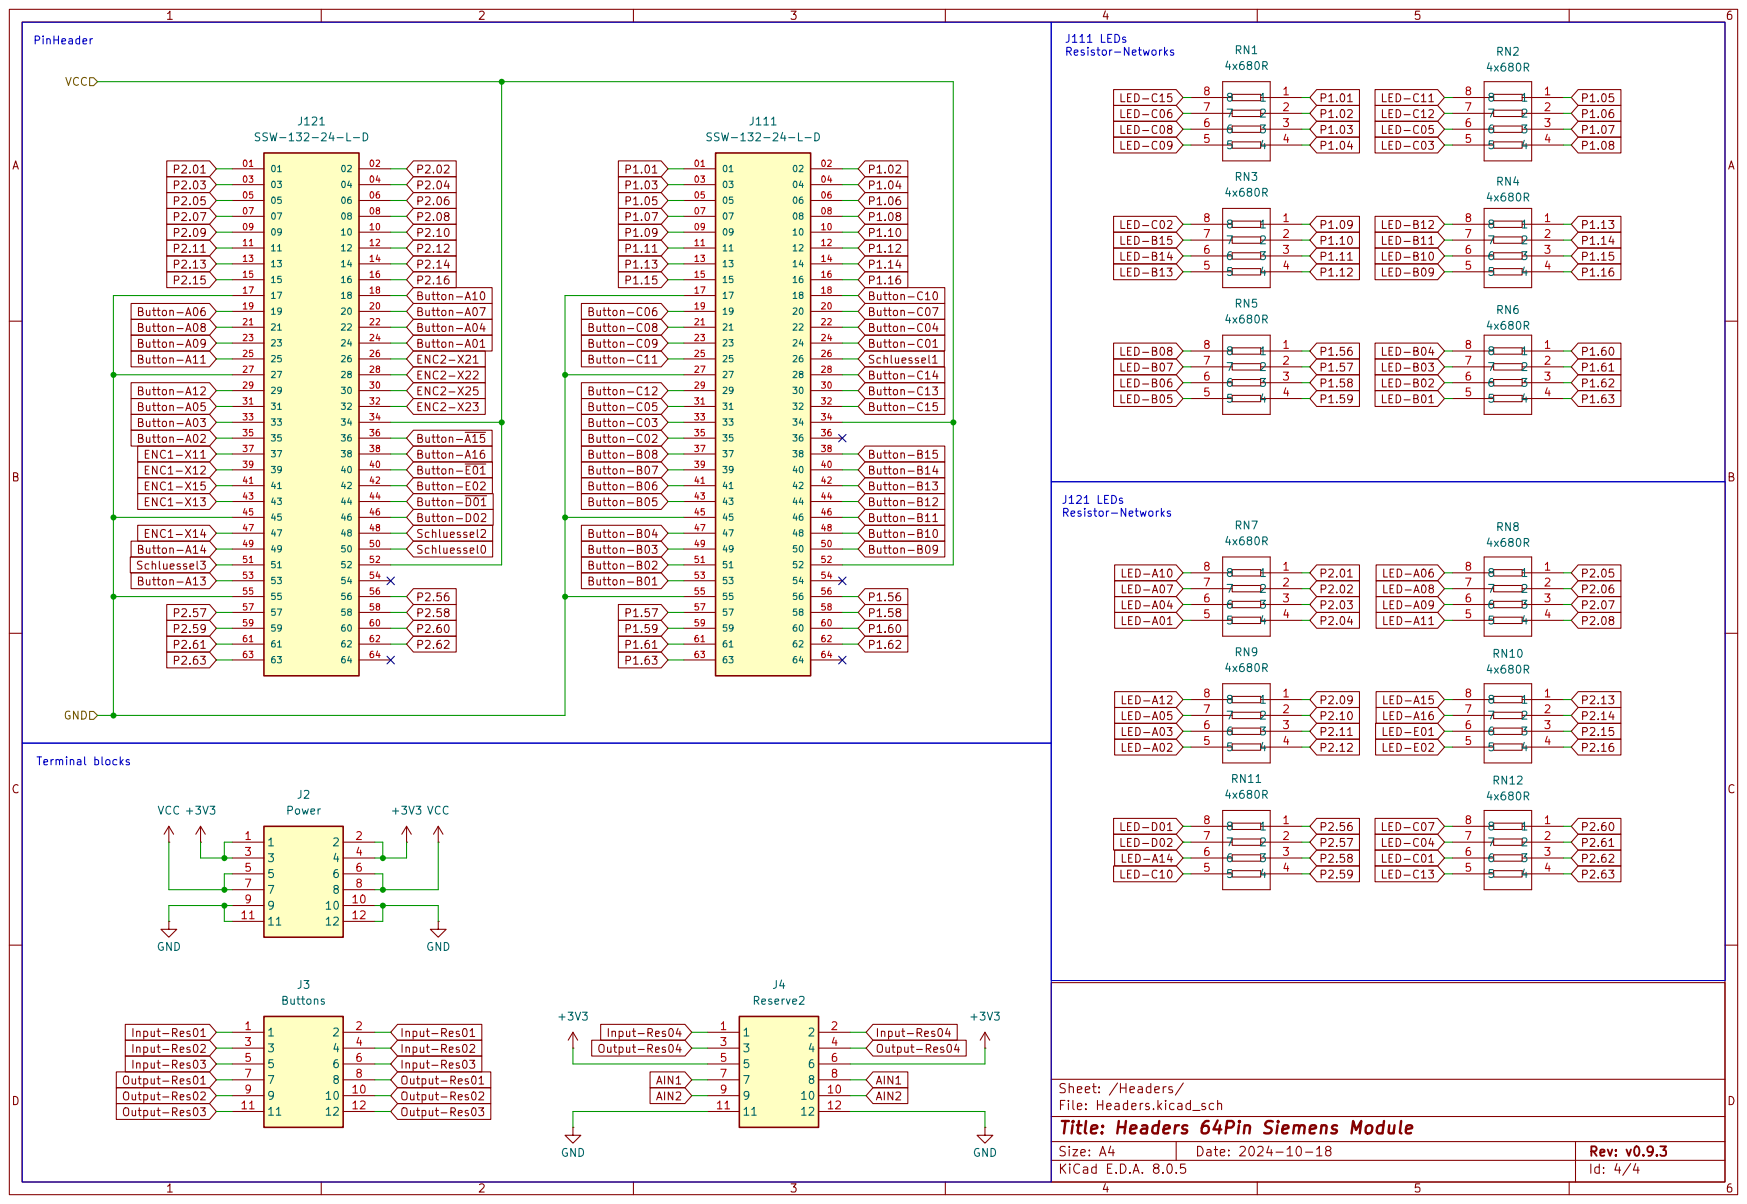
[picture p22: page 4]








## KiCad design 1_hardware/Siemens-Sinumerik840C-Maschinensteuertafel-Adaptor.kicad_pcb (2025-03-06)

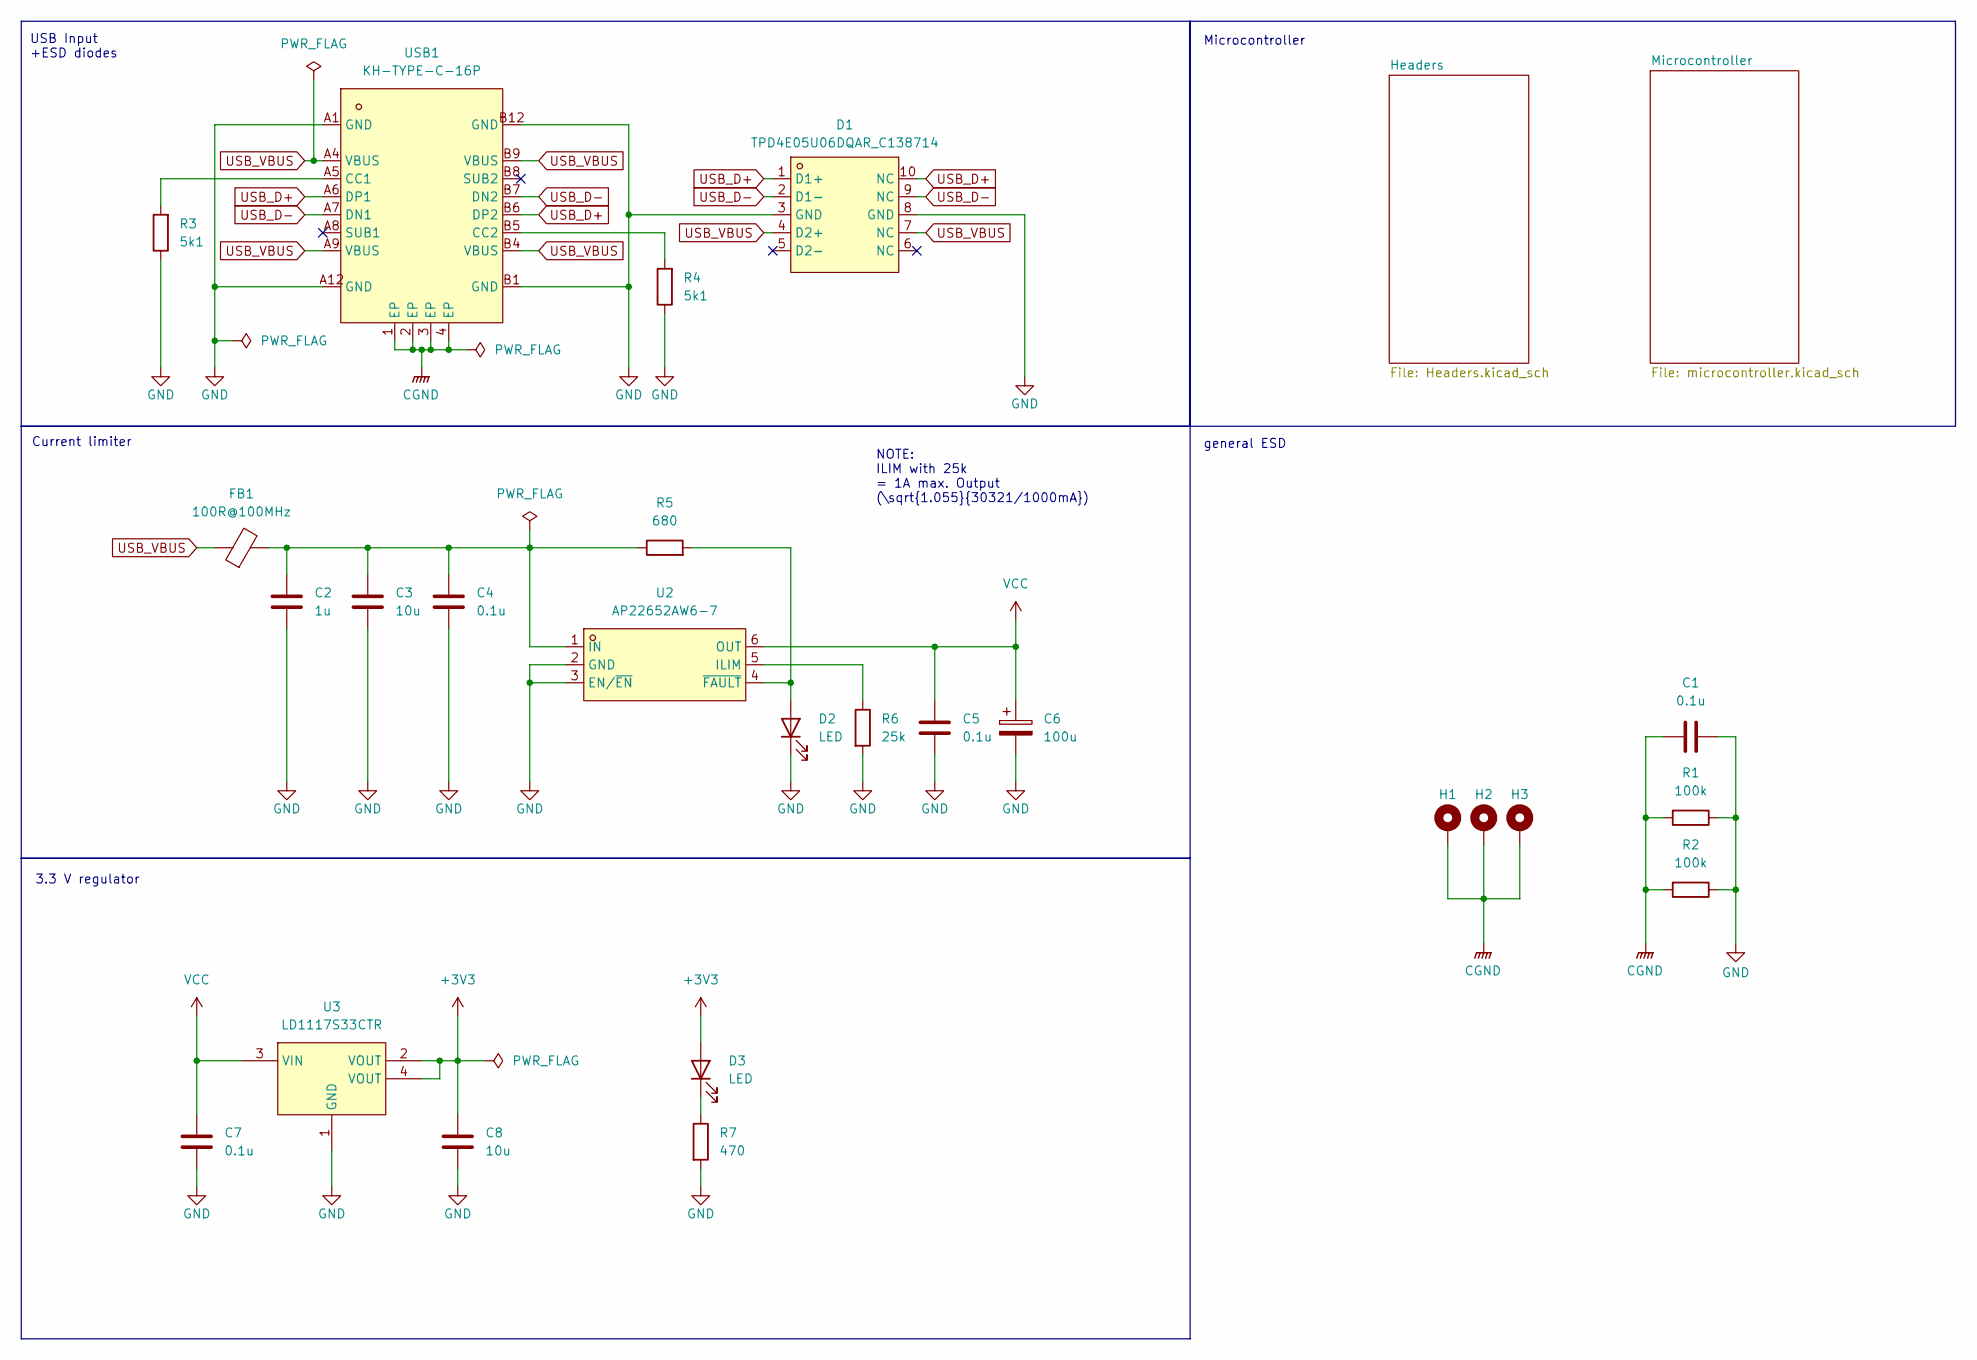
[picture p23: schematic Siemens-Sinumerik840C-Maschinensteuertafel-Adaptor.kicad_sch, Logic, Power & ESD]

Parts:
C1: 0.1u; C_2220_5750Metric; LCSC Part C5290327
C2: 1u; C_0603_1608Metric
C3, C8: 10u; C_0603_1608Metric
C4, C5, C7: 0.1u; C_0603_1608Metric
C6: 100u; CP_Elec_5x5.8; LCSC Part C336771
D1: TPD4E05U06DQAR_C138714; USON-10_L2.5-W1.0-P0.50-BL; LCSC Part C138714
D2, D3: LED; LED_0603_1608Metric
FB1: 100R@100MHz; L0603; LCSC Part C107332
H1, H2, H3: MountingHole_Pad_MP; MountingHole_3.2mm_M3_DIN965_Pad
R1, R2: 100k; R_2512_6332Metric; LCSC Part C25717
R3, R4: 5k1; R_0603_1608Metric
R5: 680; R_0603_1608Metric
R6: 25k; R_0603_1608Metric
R7: 470; R_0603_1608Metric
U2: AP22652AW6-7; SOT-23-6_L2.9-W1.6-P0.95-LS2.8-BL; LCSC Part C5329413
U3: LD1117S33CTR; SOT-223-4_L6.5-W3.5-P2.30-LS7.0-BR; LCSC Part C35879
USB1: KH-TYPE-C-16P; USB-C-SMD_KH-TYPE-C-16P; LCSC Part C709357

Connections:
+3V3: C8.2, D3.2 (A), U3.2 (VOUT), U3.4 (VOUT); also elsewhere on the board
CGND: C1.2, H1.1, H2.1, H3.1, R1.2, R2.2, USB1.1 (EP), USB1.2 (EP), USB1.3 (EP), USB1.4 (EP)
GND: C1.1, C2.1, C3.1, C4.1, C5.1, C6.2, C7.1, C8.1, D1.3 (GND), D1.8 (GND), D2.1 (K), R1.1, R2.1, R3.1, R4.1, R6.2, R7.2, U2.2 (GND), U2.3 (EN/~EN), U3.1 (GND), USB1.A1 (GND), USB1.A12 (GND), USB1.B1 (GND), USB1.B12 (GND); also elsewhere on the board
unnamed: D2.2 (A), R5.2, U2.4 (~FAULT)
unnamed: D3.1 (K), R7.1
unnamed: R6.1, U2.5 (ILIM)
unnamed: C2.2, C3.2, C4.2, FB1.2, R5.1, U2.1 (IN)
unnamed: R3.2, USB1.A5 (CC1)
unnamed: R4.2, USB1.B5 (CC2)
USB_D+: D1.1 (D1+), D1.10 (NC), USB1.A6 (DP1), USB1.B6 (DP2); also elsewhere on the board
USB_D-: D1.2 (D1-), D1.9 (NC), USB1.A7 (DN1), USB1.B7 (DN2); also elsewhere on the board
USB_VBUS: D1.4 (D2+), D1.7 (NC), FB1.1, USB1.A4 (VBUS), USB1.A9 (VBUS), USB1.B4 (VBUS), USB1.B9 (VBUS)
VCC: C5.2, C6.1, C7.2, U2.6 (OUT), U3.3 (VIN); also elsewhere on the board

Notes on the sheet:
3.3 V regulator
NOTE: ILIM with 25k = 1A max. Output (\sqrt{1.055}{30321/1000mA})
Microcontroller
Current limiter
general ESD
USB Input +ESD diodes

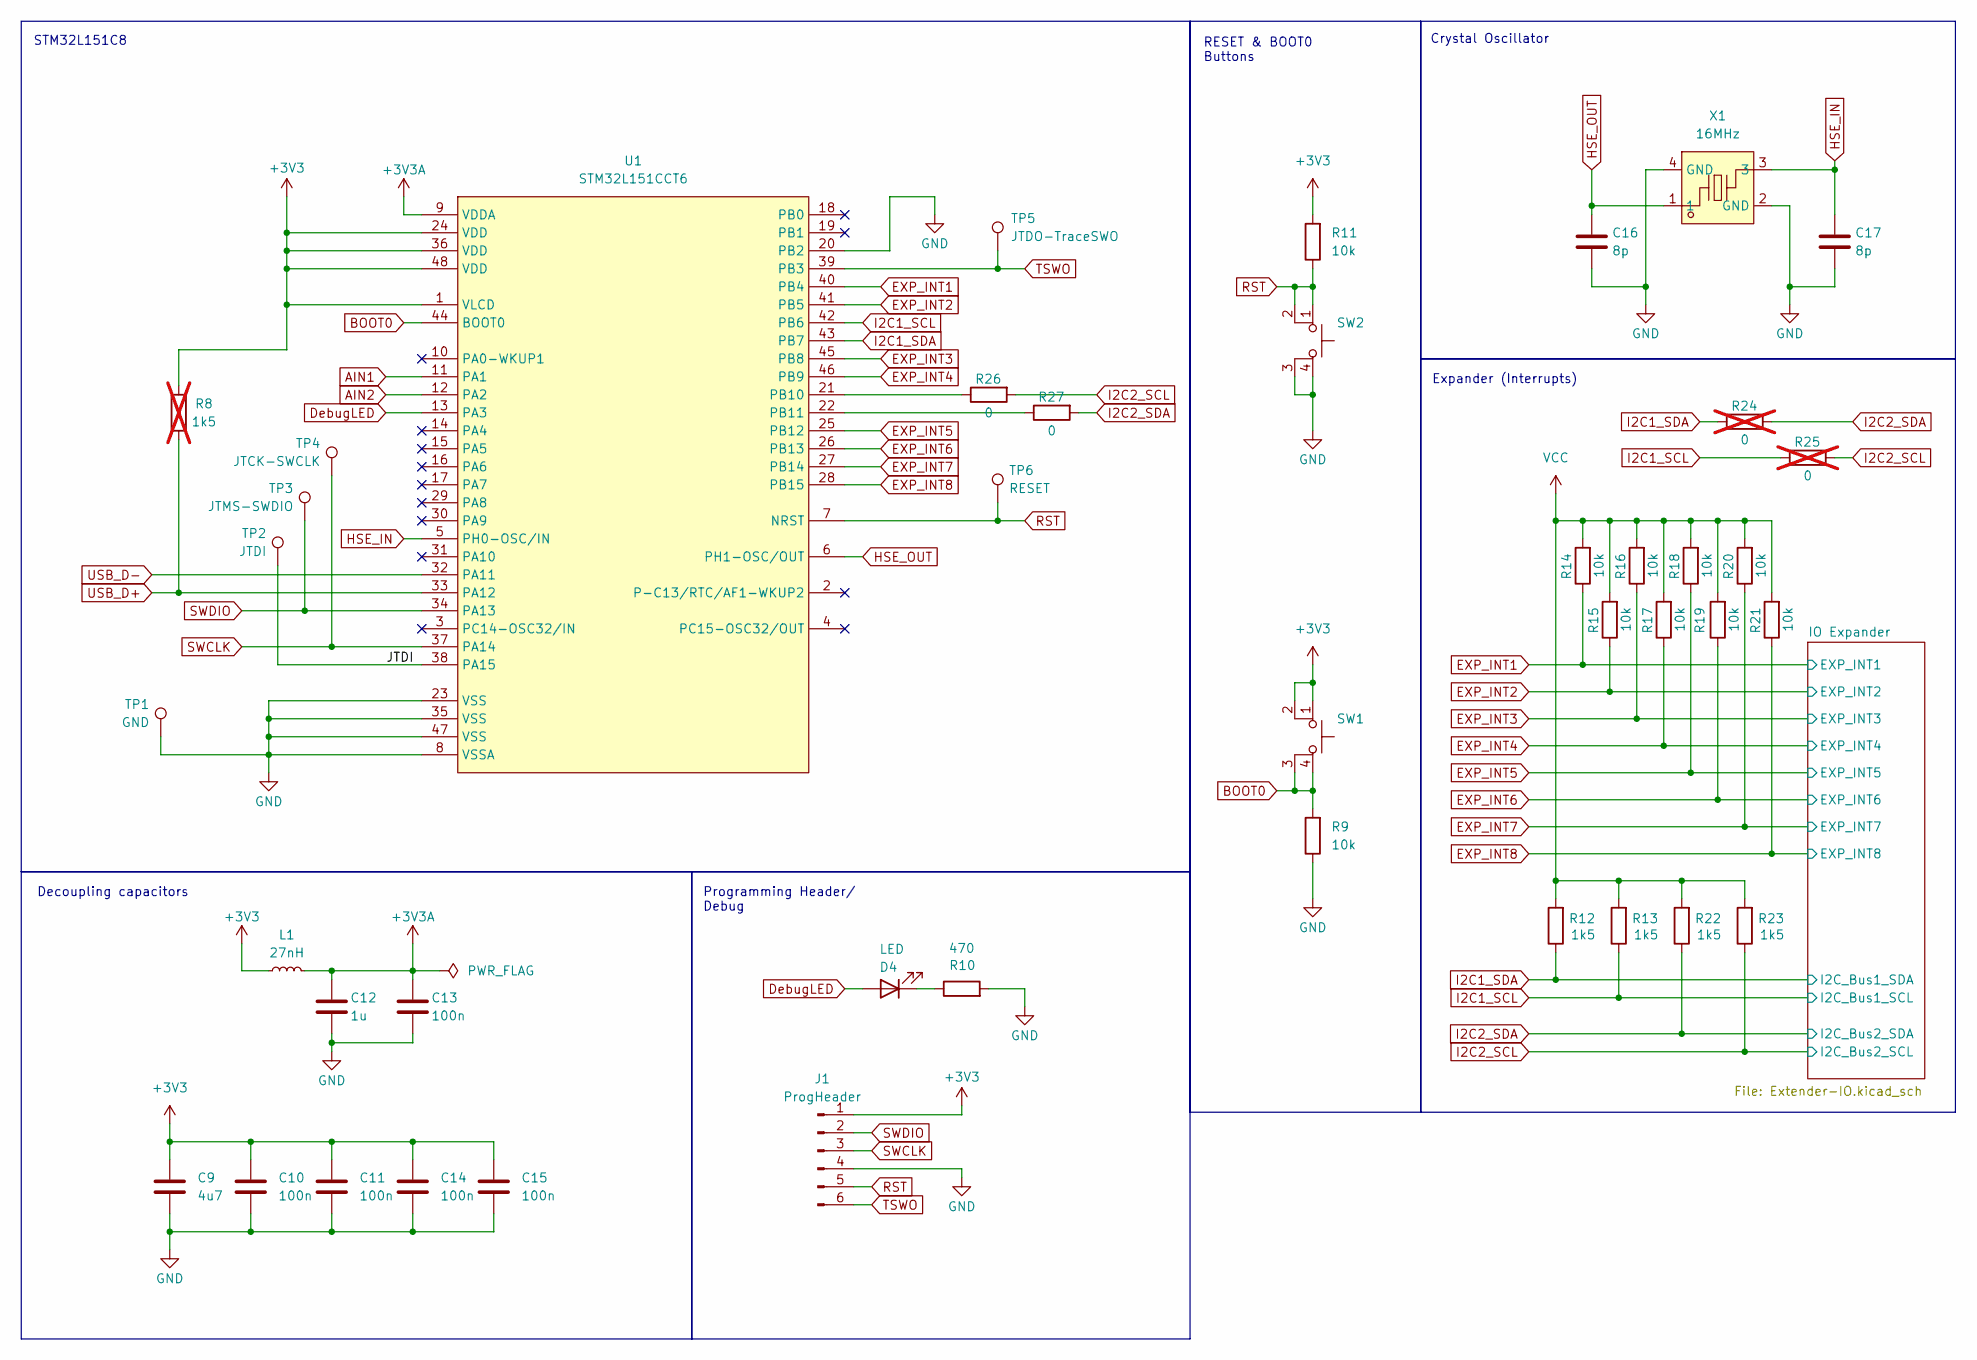
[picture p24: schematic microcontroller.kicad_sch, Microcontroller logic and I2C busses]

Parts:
C9: 4u7; C_0603_1608Metric
C10, C11, C13, C14, C15: 100n; C_0603_1608Metric
C12: 1u; C_0603_1608Metric
C16, C17: 8p; C_0603_1608Metric
D4: LED; LED_0603_1608Metric
J1: ProgHeader; HDR-SMD_6P-P2.54-V-M-LS4.8_R2; LCSC Part C2883763
L1: 27nH; L_0603_1608Metric; LCSC Part C12100
R8: 1k5; R_0603_1608Metric; not fitted
R9, R11, R14, R15, R16, R17, R18, R19, R20, R21: 10k; R_0603_1608Metric
R10: 470; R_0603_1608Metric
R12, R13, R22, R23: 1k5; R_0603_1608Metric
R24, R25: 0; R_0603_1608Metric; not fitted
R26, R27: 0; R_0603_1608Metric
SW1, SW2: TS-1187A-B-A-B; SW-SMD_4P-L5.1-W5.1-P3.70-LS6.5-TL-2; LCSC Part C318884
TP1: GND; TestPoint_Pad_D1.0mm
TP2: JTDI; TestPoint_Pad_D1.0mm
TP3: JTMS-SWDIO; TestPoint_Pad_D1.0mm
TP4: JTCK-SWCLK; TestPoint_Pad_D1.0mm
TP5: JTDO-TraceSWO; TestPoint_Pad_D1.0mm
TP6: RESET; TestPoint_Pad_D1.0mm
U1: STM32L151CCT6; LQFP-48_L7.0-W7.0-P0.50-LS9.0-BL; LCSC Part C2149675
X1: 16MHz; CRYSTAL-SMD_4P-L3.2-W2.5-BL_SIT8008BI; LCSC Part C498200

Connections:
+3V3: C9.2, C10.2, C11.2, C14.2, C15.2, J1.1, L1.1, R8.1, R11.2, SW1.1, SW1.2, U1.1 (VLCD), U1.24 (VDD), U1.36 (VDD), U1.48 (VDD); also elsewhere on the board
+3V3A: C12.2, C13.2, L1.2, U1.9 (VDDA)
/Microcontroller/JTDI: TP2.1, U1.38 (PA15)
AIN1: U1.11 (PA1); also elsewhere on the board
AIN2: U1.12 (PA2); also elsewhere on the board
BOOT0: R9.2, SW1.3 (K), SW1.4 (A), U1.44 (BOOT0)
DebugLED: D4.2 (A), U1.13 (PA3)
EXP_INT1: R14.1, U1.40 (PB4); also elsewhere on the board
EXP_INT2: R15.1, U1.41 (PB5); also elsewhere on the board
EXP_INT3: R16.1, U1.45 (PB8); also elsewhere on the board
EXP_INT4: R17.1, U1.46 (PB9); also elsewhere on the board
EXP_INT5: R18.1, U1.25 (PB12); also elsewhere on the board
EXP_INT6: R19.1, U1.26 (PB13); also elsewhere on the board
EXP_INT7: R20.1, U1.27 (PB14); also elsewhere on the board
EXP_INT8: R21.1, U1.28 (PB15); also elsewhere on the board
GND: C9.1, C10.1, C11.1, C12.1, C13.1, C14.1, C15.1, C16.1, C17.1, J1.4, R9.1, R10.2, SW2.3 (K), SW2.4 (A), TP1.1, U1.8 (VSSA), U1.20 (PB2), U1.23 (VSS), U1.35 (VSS), U1.47 (VSS), X1.2 (GND), X1.4 (GND); also elsewhere on the board
HSE_IN: C17.2, U1.5 (PH0-OSC/IN), X1.3
HSE_OUT: C16.2, U1.6 (PH1-OSC/OUT), X1.1
I2C1_SCL: R13.1, R25.1, U1.42 (PB6); also elsewhere on the board
I2C1_SDA: R12.1, R24.1, U1.43 (PB7); also elsewhere on the board
I2C2_SCL: R23.1, R25.2, R26.2; also elsewhere on the board
I2C2_SDA: R22.1, R24.2, R27.2; also elsewhere on the board
unnamed: D4.1 (K), R10.1
unnamed: R26.1, U1.21 (PB10)
unnamed: R27.1, U1.22 (PB11)
RST: J1.5, R11.1, SW2.1, SW2.2, TP6.1, U1.7 (NRST)
SWCLK: J1.3, TP4.1, U1.37 (PA14)
SWDIO: J1.2, TP3.1, U1.34 (PA13)
TSWO: J1.6, TP5.1, U1.39 (PB3)
USB_D+: R8.2, U1.33 (PA12); also elsewhere on the board
USB_D-: U1.32 (PA11); also elsewhere on the board
VCC: R12.2, R13.2, R14.2, R15.2, R16.2, R17.2, R18.2, R19.2, R20.2, R21.2, R22.2, R23.2; also elsewhere on the board

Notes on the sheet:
STM32L151C8
RESET & BOOT0 Buttons
Crystal Oscillator
Decoupling capacitors
Programming Header/ Debug
Expander (Interrupts)

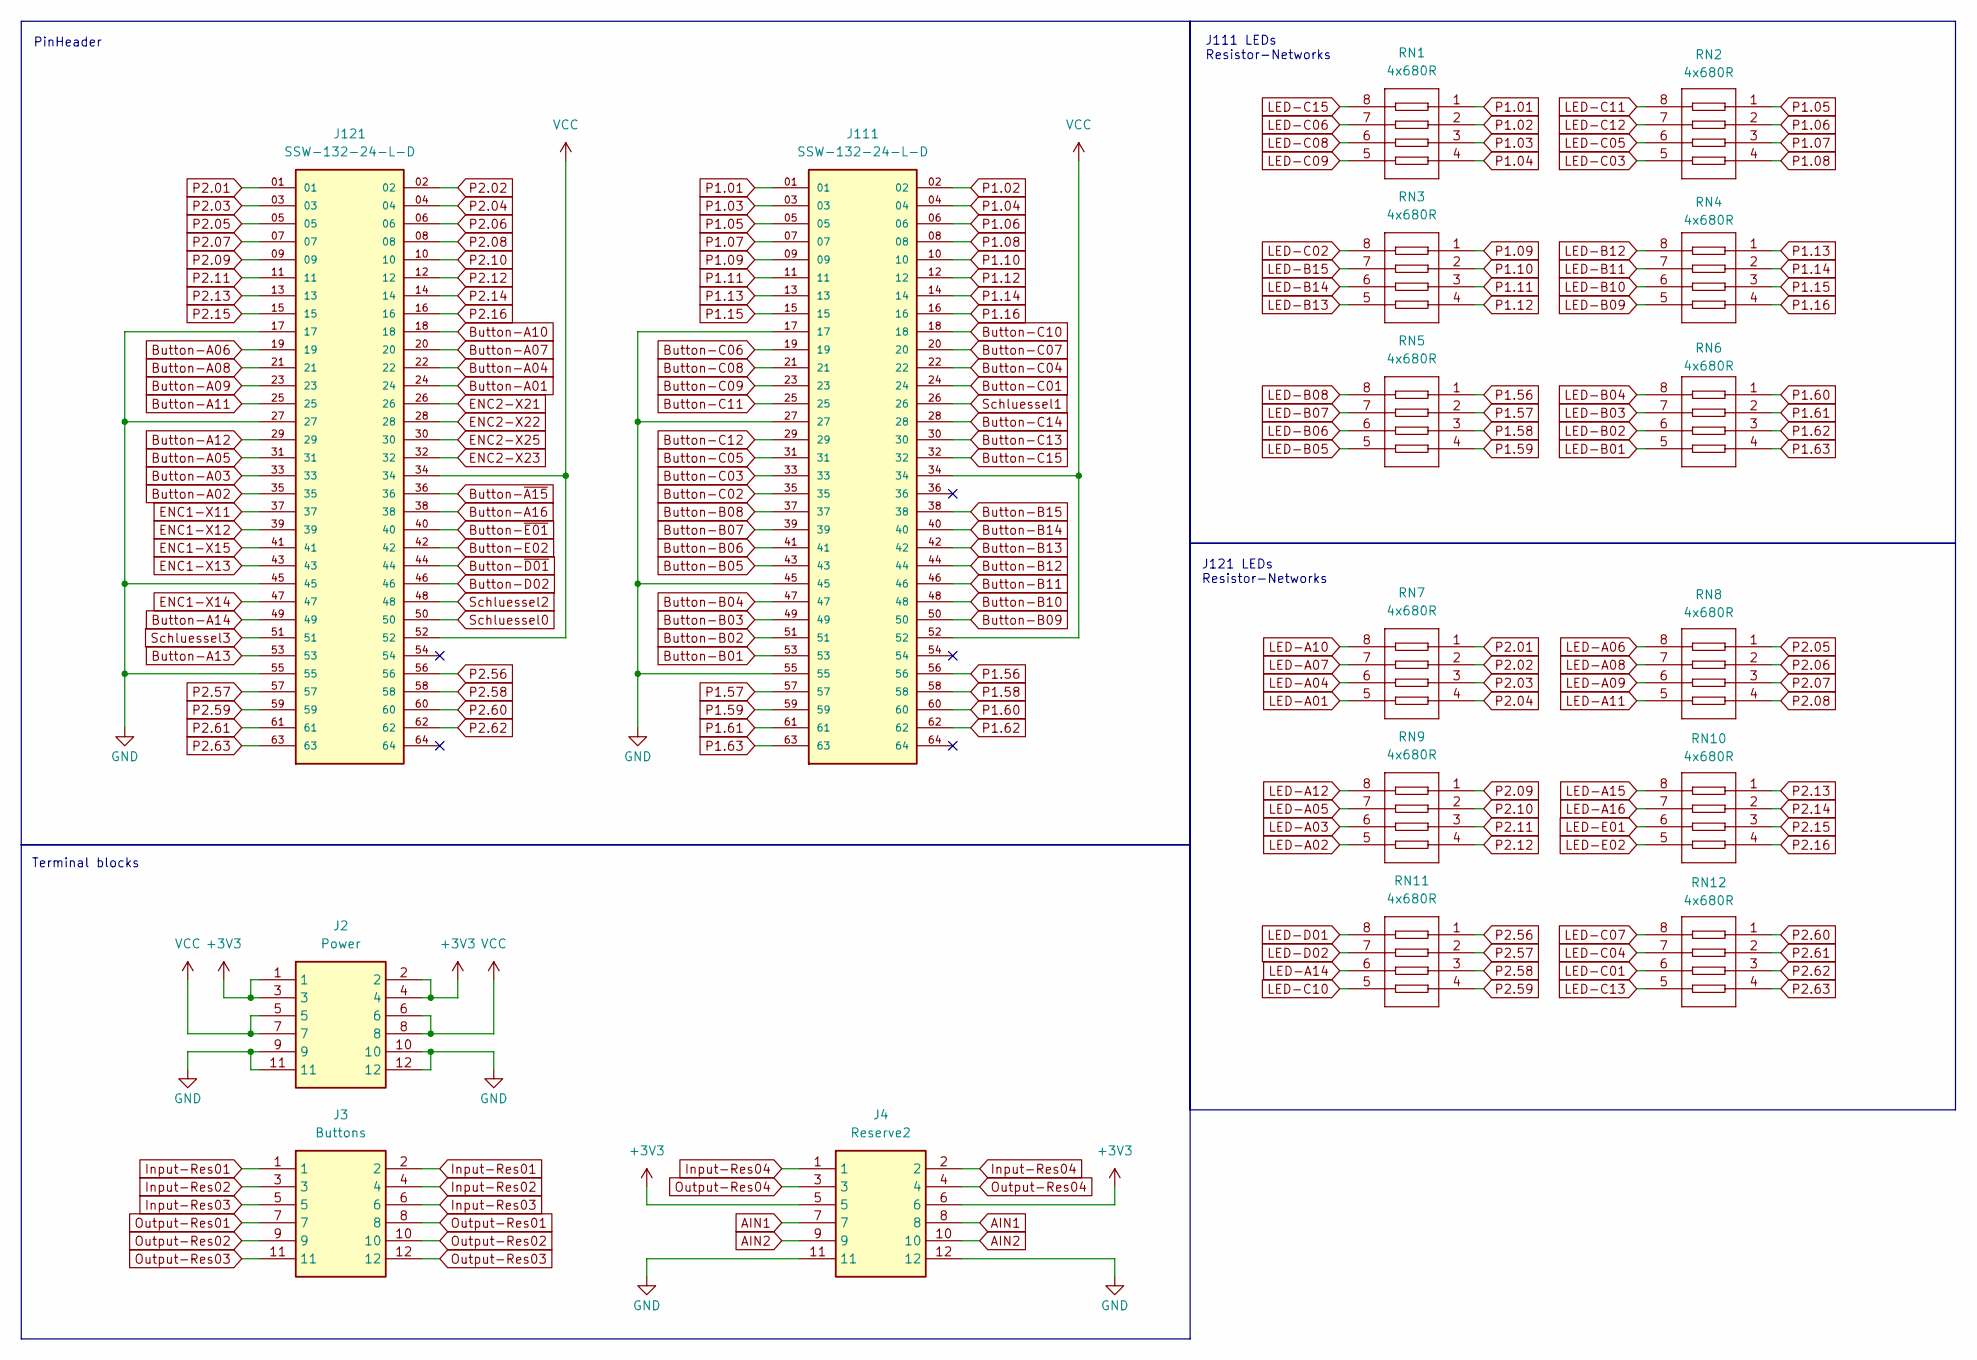
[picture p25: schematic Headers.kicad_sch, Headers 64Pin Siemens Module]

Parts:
J2: Power; 1824460000 - LSF-SMT 3.500690 3.5SN BK TU; Manufacturer_Part_Number 1824460000; Mouser Part Number 470-1824460000
J3: Buttons; 1824460000 - LSF-SMT 3.500690 3.5SN BK TU; Manufacturer_Part_Number 1824460000; Mouser Part Number 470-1824460000
J4: Reserve2; 1824460000 - LSF-SMT 3.500690 3.5SN BK TU; Manufacturer_Part_Number 1824460000; Mouser Part Number 470-1824460000
J111, J121: SSW-132-24-L-D; SAMTEC_SSW-132-24-L-D; PARTREV R
RN1, RN2, RN3, RN4, RN5, RN6, RN7, RN8, RN9, RN10, RN11, RN12: 4x680R; RES-ARRAY-SMD_0603-8P-L3.2-W1.6-BL; LCSC Part C12035

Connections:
+3V3: J2.1, J2.2, J2.3, J2.4, J4.5, J4.6; also elsewhere on the board
AIN1: J4.7, J4.8; also elsewhere on the board
AIN2: J4.9, J4.10; also elsewhere on the board
Button-A01: J121.24; also elsewhere on the board
Button-A02: J121.35; also elsewhere on the board
Button-A03: J121.33; also elsewhere on the board
Button-A04: J121.22; also elsewhere on the board
Button-A05: J121.31; also elsewhere on the board
Button-A06: J121.19; also elsewhere on the board
Button-A07: J121.20; also elsewhere on the board
Button-A08: J121.21; also elsewhere on the board
Button-A09: J121.23; also elsewhere on the board
Button-A10: J121.18; also elsewhere on the board
Button-A11: J121.25; also elsewhere on the board
Button-A12: J121.29; also elsewhere on the board
Button-A13: J121.53; also elsewhere on the board
Button-A14: J121.49; also elsewhere on the board
Button-A16: J121.38; also elsewhere on the board
Button-B01: J111.53; also elsewhere on the board
Button-B02: J111.51; also elsewhere on the board
Button-B03: J111.49; also elsewhere on the board
Button-B04: J111.47; also elsewhere on the board
Button-B05: J111.43; also elsewhere on the board
Button-B06: J111.41; also elsewhere on the board
Button-B07: J111.39; also elsewhere on the board
Button-B08: J111.37; also elsewhere on the board
Button-B09: J111.50; also elsewhere on the board
Button-B10: J111.48; also elsewhere on the board
Button-B11: J111.46; also elsewhere on the board
Button-B12: J111.44; also elsewhere on the board
Button-B13: J111.42; also elsewhere on the board
Button-B14: J111.40; also elsewhere on the board
Button-B15: J111.38; also elsewhere on the board
Button-C01: J111.24; also elsewhere on the board
Button-C02: J111.35; also elsewhere on the board
Button-C03: J111.33; also elsewhere on the board
Button-C04: J111.22; also elsewhere on the board
Button-C05: J111.31; also elsewhere on the board
Button-C06: J111.19; also elsewhere on the board
Button-C07: J111.20; also elsewhere on the board
Button-C08: J111.21; also elsewhere on the board
Button-C09: J111.23; also elsewhere on the board
Button-C10: J111.18; also elsewhere on the board
Button-C11: J111.25; also elsewhere on the board
Button-C12: J111.29; also elsewhere on the board
Button-C13: J111.30; also elsewhere on the board
Button-C14: J111.28; also elsewhere on the board
Button-C15: J111.32; also elsewhere on the board
Button-D02: J121.46; also elsewhere on the board
Button-E02: J121.42; also elsewhere on the board
Button-~A15: J121.36; also elsewhere on the board
Button-~D01: J121.44; also elsewhere on the board
Button-~E01: J121.40; also elsewhere on the board
ENC1-X11: J121.37; also elsewhere on the board
ENC1-X12: J121.39; also elsewhere on the board
ENC1-X13: J121.43; also elsewhere on the board
ENC1-X14: J121.47; also elsewhere on the board
ENC1-X15: J121.41; also elsewhere on the board
ENC2-X21: J121.26; also elsewhere on the board
ENC2-X22: J121.28; also elsewhere on the board
ENC2-X23: J121.32; also elsewhere on the board
ENC2-X25: J121.30; also elsewhere on the board
GND: J2.9, J2.10, J2.11, J2.12, J4.11, J4.12, J111.17, J111.27, J111.45, J111.55, J121.17, J121.27, J121.45, J121.55; also elsewhere on the board
Input-Res01: J3.1, J3.2; also elsewhere on the board
Input-Res02: J3.3, J3.4; also elsewhere on the board
Input-Res03: J3.5, J3.6; also elsewhere on the board
Input-Res04: J4.1, J4.2; also elsewhere on the board
LED-A01: RN7.5; also elsewhere on the board
LED-A02: RN9.5; also elsewhere on the board
LED-A03: RN9.6; also elsewhere on the board
LED-A04: RN7.6; also elsewhere on the board
LED-A05: RN9.7; also elsewhere on the board
LED-A06: RN8.8; also elsewhere on the board
LED-A07: RN7.7; also elsewhere on the board
LED-A08: RN8.7; also elsewhere on the board
LED-A09: RN8.6; also elsewhere on the board
LED-A10: RN7.8; also elsewhere on the board
LED-A11: RN8.5; also elsewhere on the board
LED-A12: RN9.8; also elsewhere on the board
LED-A14: RN11.6; also elsewhere on the board
LED-A15: RN10.8; also elsewhere on the board
LED-A16: RN10.7; also elsewhere on the board
LED-B01: RN6.5; also elsewhere on the board
LED-B02: RN6.6; also elsewhere on the board
LED-B03: RN6.7; also elsewhere on the board
LED-B04: RN6.8; also elsewhere on the board
LED-B05: RN5.5; also elsewhere on the board
LED-B06: RN5.6; also elsewhere on the board
LED-B07: RN5.7; also elsewhere on the board
LED-B08: RN5.8; also elsewhere on the board
LED-B09: RN4.5; also elsewhere on the board
LED-B10: RN4.6; also elsewhere on the board
LED-B11: RN4.7; also elsewhere on the board
LED-B12: RN4.8; also elsewhere on the board
LED-B13: RN3.5; also elsewhere on the board
LED-B14: RN3.6; also elsewhere on the board
LED-B15: RN3.7; also elsewhere on the board
LED-C01: RN12.6; also elsewhere on the board
LED-C02: RN3.8; also elsewhere on the board
LED-C03: RN2.5; also elsewhere on the board
LED-C04: RN12.7; also elsewhere on the board
LED-C05: RN2.6; also elsewhere on the board
LED-C06: RN1.7; also elsewhere on the board
LED-C07: RN12.8; also elsewhere on the board
LED-C08: RN1.6; also elsewhere on the board
LED-C09: RN1.5; also elsewhere on the board
LED-C10: RN11.5; also elsewhere on the board
LED-C11: RN2.8; also elsewhere on the board
LED-C12: RN2.7; also elsewhere on the board
LED-C13: RN12.5; also elsewhere on the board
LED-C15: RN1.8; also elsewhere on the board
LED-D01: RN11.8; also elsewhere on the board
LED-D02: RN11.7; also elsewhere on the board
LED-E01: RN10.6; also elsewhere on the board
LED-E02: RN10.5; also elsewhere on the board
Output-Res01: J3.7, J3.8; also elsewhere on the board
Output-Res02: J3.9, J3.10; also elsewhere on the board
Output-Res03: J3.11, J3.12; also elsewhere on the board
Output-Res04: J4.3, J4.4; also elsewhere on the board
P1.01: J111.01, RN1.1
P1.02: J111.02, RN1.2
P1.03: J111.03, RN1.3
P1.04: J111.04, RN1.4
P1.05: J111.05, RN2.1
P1.06: J111.06, RN2.2
P1.07: J111.07, RN2.3
P1.08: J111.08, RN2.4
P1.09: J111.09, RN3.1
P1.10: J111.10, RN3.2
P1.11: J111.11, RN3.3
P1.12: J111.12, RN3.4
P1.13: J111.13, RN4.1
P1.14: J111.14, RN4.2
P1.15: J111.15, RN4.3
P1.16: J111.16, RN4.4
P1.56: J111.56, RN5.1
P1.57: J111.57, RN5.2
P1.58: J111.58, RN5.3
P1.59: J111.59, RN5.4
P1.60: J111.60, RN6.1
P1.61: J111.61, RN6.2
P1.62: J111.62, RN6.3
P1.63: J111.63, RN6.4
P2.01: J121.01, RN7.1
P2.02: J121.02, RN7.2
P2.03: J121.03, RN7.3
P2.04: J121.04, RN7.4
P2.05: J121.05, RN8.1
P2.06: J121.06, RN8.2
P2.07: J121.07, RN8.3
P2.08: J121.08, RN8.4
P2.09: J121.09, RN9.1
P2.10: J121.10, RN9.2
P2.11: J121.11, RN9.3
P2.12: J121.12, RN9.4
P2.13: J121.13, RN10.1
P2.14: J121.14, RN10.2
P2.15: J121.15, RN10.3
P2.16: J121.16, RN10.4
P2.56: J121.56, RN11.1
P2.57: J121.57, RN11.2
P2.58: J121.58, RN11.3
P2.59: J121.59, RN11.4
P2.60: J121.60, RN12.1
P2.61: J121.61, RN12.2
P2.62: J121.62, RN12.3
P2.63: J121.63, RN12.4
Schluessel0: J121.50; also elsewhere on the board
Schluessel1: J111.26; also elsewhere on the board
Schluessel2: J121.48; also elsewhere on the board
Schluessel3: J121.51; also elsewhere on the board
VCC: J2.5, J2.6, J2.7, J2.8, J111.34, J111.52, J121.34, J121.52; also elsewhere on the board

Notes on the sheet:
Terminal blocks
J121 LEDs Resistor-Networks
PinHeader
J111 LEDs Resistor-Networks

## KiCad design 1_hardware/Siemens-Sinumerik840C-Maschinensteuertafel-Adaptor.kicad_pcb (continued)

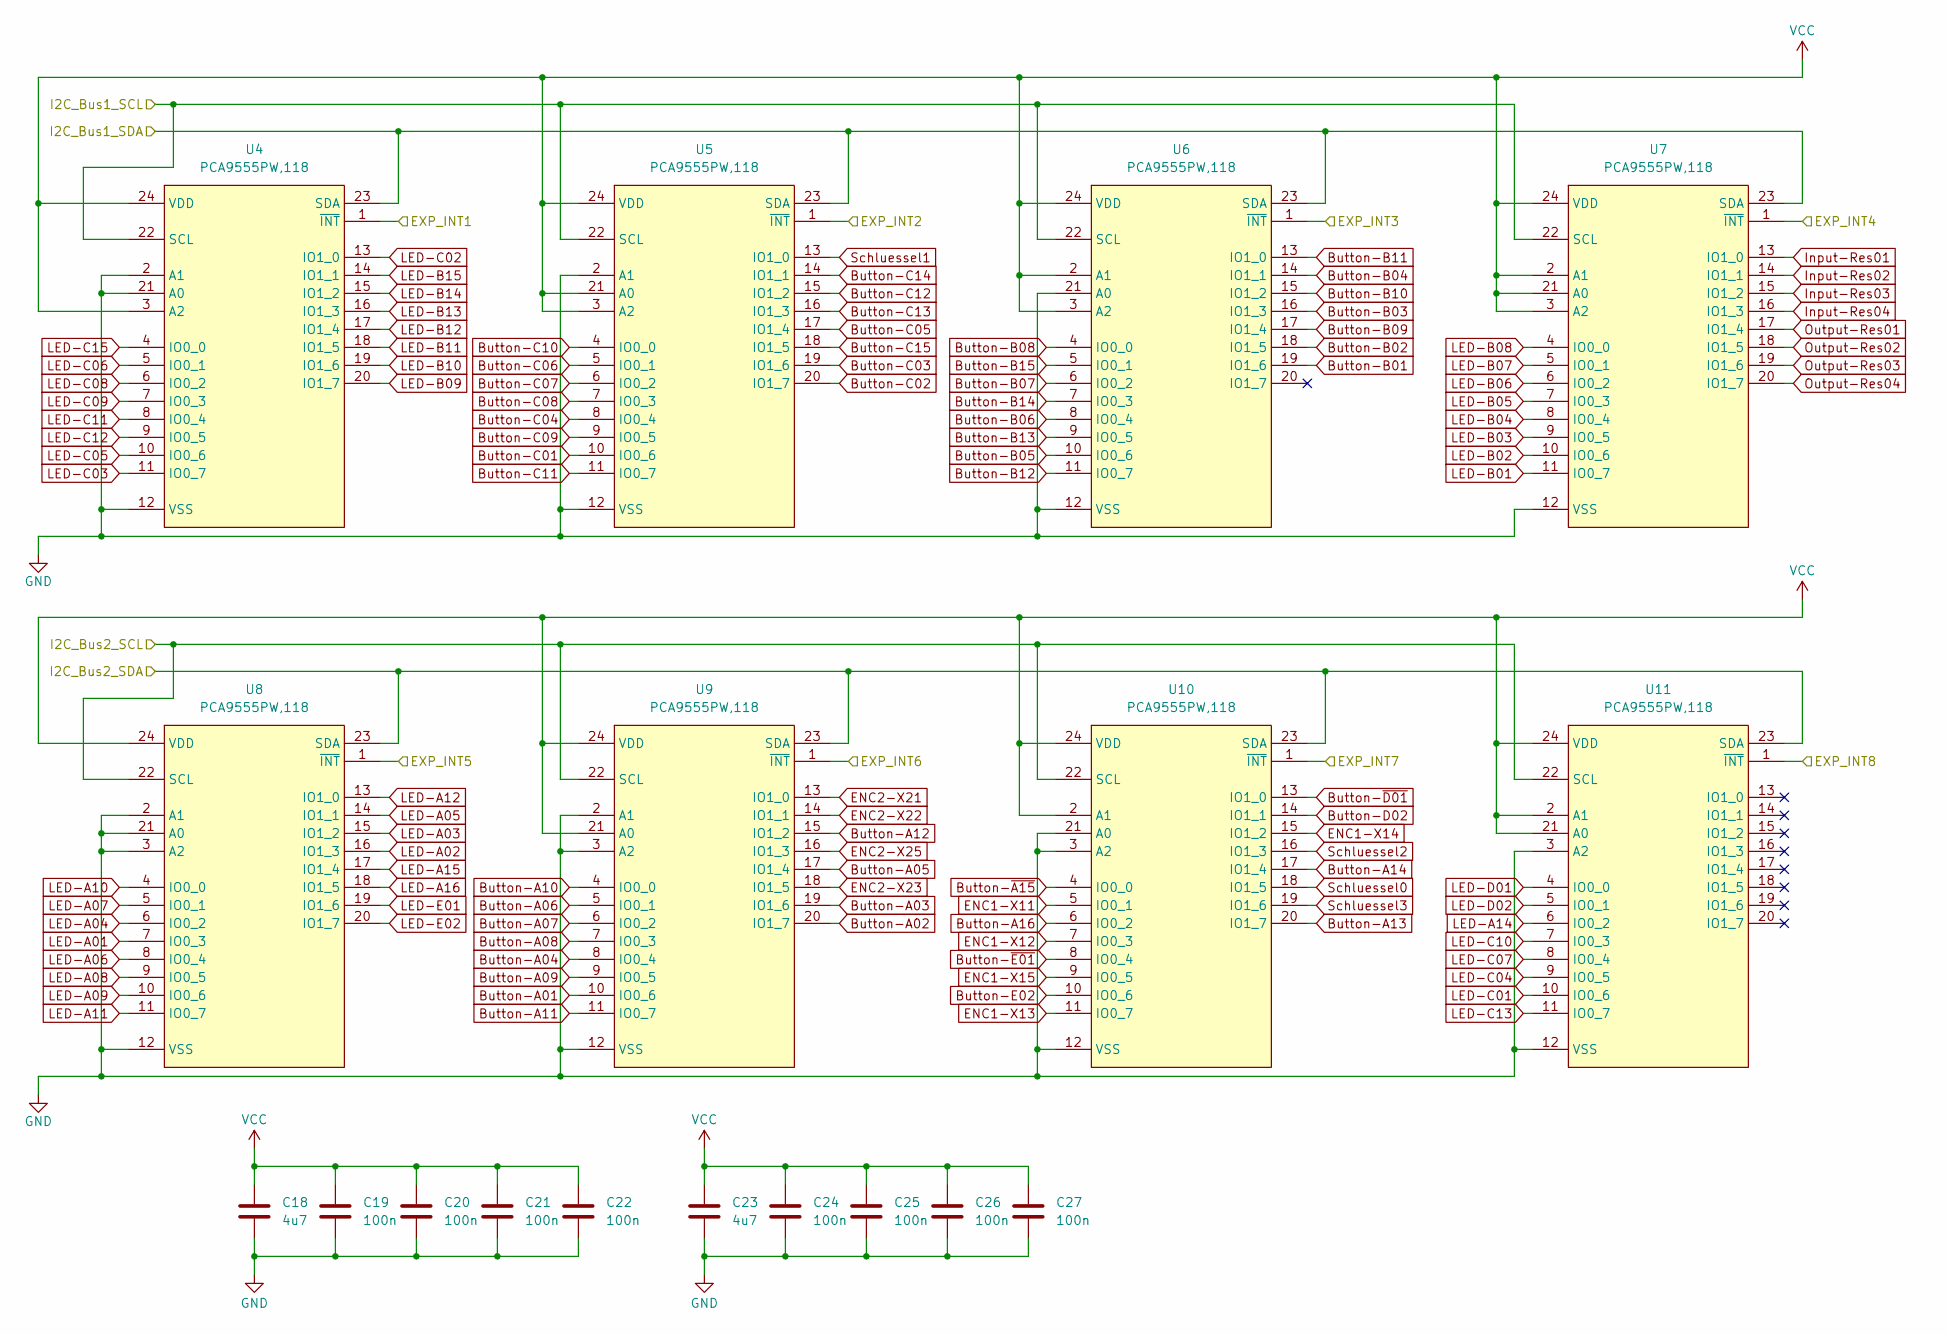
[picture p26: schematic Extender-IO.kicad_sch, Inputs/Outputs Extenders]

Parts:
C18, C23: 4u7; C_0603_1608Metric
C19, C20, C21, C22, C24, C25, C26, C27: 100n; C_0603_1608Metric
U4, U5, U6, U7, U8, U9, U10, U11: PCA9555PW,118; TSSOP-24_L7.8-W4.4-P0.65-LS6.4-BL; LCSC Part C128392

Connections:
Button-A01: U9.10 (IO0_6); also elsewhere on the board
Button-A02: U9.20 (IO1_7); also elsewhere on the board
Button-A03: U9.19 (IO1_6); also elsewhere on the board
Button-A04: U9.8 (IO0_4); also elsewhere on the board
Button-A05: U9.17 (IO1_4); also elsewhere on the board
Button-A06: U9.5 (IO0_1); also elsewhere on the board
Button-A07: U9.6 (IO0_2); also elsewhere on the board
Button-A08: U9.7 (IO0_3); also elsewhere on the board
Button-A09: U9.9 (IO0_5); also elsewhere on the board
Button-A10: U9.4 (IO0_0); also elsewhere on the board
Button-A11: U9.11 (IO0_7); also elsewhere on the board
Button-A12: U9.15 (IO1_2); also elsewhere on the board
Button-A13: U10.20 (IO1_7); also elsewhere on the board
Button-A14: U10.17 (IO1_4); also elsewhere on the board
Button-A16: U10.6 (IO0_2); also elsewhere on the board
Button-B01: U6.19 (IO1_6); also elsewhere on the board
Button-B02: U6.18 (IO1_5); also elsewhere on the board
Button-B03: U6.16 (IO1_3); also elsewhere on the board
Button-B04: U6.14 (IO1_1); also elsewhere on the board
Button-B05: U6.10 (IO0_6); also elsewhere on the board
Button-B06: U6.8 (IO0_4); also elsewhere on the board
Button-B07: U6.6 (IO0_2); also elsewhere on the board
Button-B08: U6.4 (IO0_0); also elsewhere on the board
Button-B09: U6.17 (IO1_4); also elsewhere on the board
Button-B10: U6.15 (IO1_2); also elsewhere on the board
Button-B11: U6.13 (IO1_0); also elsewhere on the board
Button-B12: U6.11 (IO0_7); also elsewhere on the board
Button-B13: U6.9 (IO0_5); also elsewhere on the board
Button-B14: U6.7 (IO0_3); also elsewhere on the board
Button-B15: U6.5 (IO0_1); also elsewhere on the board
Button-C01: U5.10 (IO0_6); also elsewhere on the board
Button-C02: U5.20 (IO1_7); also elsewhere on the board
Button-C03: U5.19 (IO1_6); also elsewhere on the board
Button-C04: U5.8 (IO0_4); also elsewhere on the board
Button-C05: U5.17 (IO1_4); also elsewhere on the board
Button-C06: U5.5 (IO0_1); also elsewhere on the board
Button-C07: U5.6 (IO0_2); also elsewhere on the board
Button-C08: U5.7 (IO0_3); also elsewhere on the board
Button-C09: U5.9 (IO0_5); also elsewhere on the board
Button-C10: U5.4 (IO0_0); also elsewhere on the board
Button-C11: U5.11 (IO0_7); also elsewhere on the board
Button-C12: U5.15 (IO1_2); also elsewhere on the board
Button-C13: U5.16 (IO1_3); also elsewhere on the board
Button-C14: U5.14 (IO1_1); also elsewhere on the board
Button-C15: U5.18 (IO1_5); also elsewhere on the board
Button-D02: U10.14 (IO1_1); also elsewhere on the board
Button-E02: U10.10 (IO0_6); also elsewhere on the board
Button-~A15: U10.4 (IO0_0); also elsewhere on the board
Button-~D01: U10.13 (IO1_0); also elsewhere on the board
Button-~E01: U10.8 (IO0_4); also elsewhere on the board
ENC1-X11: U10.5 (IO0_1); also elsewhere on the board
ENC1-X12: U10.7 (IO0_3); also elsewhere on the board
ENC1-X13: U10.11 (IO0_7); also elsewhere on the board
ENC1-X14: U10.15 (IO1_2); also elsewhere on the board
ENC1-X15: U10.9 (IO0_5); also elsewhere on the board
ENC2-X21: U9.13 (IO1_0); also elsewhere on the board
ENC2-X22: U9.14 (IO1_1); also elsewhere on the board
ENC2-X23: U9.18 (IO1_5); also elsewhere on the board
ENC2-X25: U9.16 (IO1_3); also elsewhere on the board
EXP_INT1: U4.1 (~INT); also elsewhere on the board
EXP_INT2: U5.1 (~INT); also elsewhere on the board
EXP_INT3: U6.1 (~INT); also elsewhere on the board
EXP_INT4: U7.1 (~INT); also elsewhere on the board
EXP_INT5: U8.1 (~INT); also elsewhere on the board
EXP_INT6: U9.1 (~INT); also elsewhere on the board
EXP_INT7: U10.1 (~INT); also elsewhere on the board
EXP_INT8: U11.1 (~INT); also elsewhere on the board
GND: C18.1, C19.1, C20.1, C21.1, C22.1, C23.1, C24.1, C25.1, C26.1, C27.1, U4.2 (A1), U4.12 (VSS), U4.21 (A0), U5.2 (A1), U5.12 (VSS), U6.12 (VSS), U6.21 (A0), U7.12 (VSS), U8.2 (A1), U8.3 (A2), U8.12 (VSS), U8.21 (A0), U9.2 (A1), U9.3 (A2), U9.12 (VSS), U10.3 (A2), U10.12 (VSS), U10.21 (A0), U11.3 (A2), U11.12 (VSS); also elsewhere on the board
I2C1_SCL: U4.22 (SCL), U5.22 (SCL), U6.22 (SCL), U7.22 (SCL); also elsewhere on the board
I2C1_SDA: U4.23 (SDA), U5.23 (SDA), U6.23 (SDA), U7.23 (SDA); also elsewhere on the board
I2C2_SCL: U8.22 (SCL), U9.22 (SCL), U10.22 (SCL), U11.22 (SCL); also elsewhere on the board
I2C2_SDA: U8.23 (SDA), U9.23 (SDA), U10.23 (SDA), U11.23 (SDA); also elsewhere on the board
Input-Res01: U7.13 (IO1_0); also elsewhere on the board
Input-Res02: U7.14 (IO1_1); also elsewhere on the board
Input-Res03: U7.15 (IO1_2); also elsewhere on the board
Input-Res04: U7.16 (IO1_3); also elsewhere on the board
LED-A01: U8.7 (IO0_3); also elsewhere on the board
LED-A02: U8.16 (IO1_3); also elsewhere on the board
LED-A03: U8.15 (IO1_2); also elsewhere on the board
LED-A04: U8.6 (IO0_2); also elsewhere on the board
LED-A05: U8.14 (IO1_1); also elsewhere on the board
LED-A06: U8.8 (IO0_4); also elsewhere on the board
LED-A07: U8.5 (IO0_1); also elsewhere on the board
LED-A08: U8.9 (IO0_5); also elsewhere on the board
LED-A09: U8.10 (IO0_6); also elsewhere on the board
LED-A10: U8.4 (IO0_0); also elsewhere on the board
LED-A11: U8.11 (IO0_7); also elsewhere on the board
LED-A12: U8.13 (IO1_0); also elsewhere on the board
LED-A14: U11.6 (IO0_2); also elsewhere on the board
LED-A15: U8.17 (IO1_4); also elsewhere on the board
LED-A16: U8.18 (IO1_5); also elsewhere on the board
LED-B01: U7.11 (IO0_7); also elsewhere on the board
LED-B02: U7.10 (IO0_6); also elsewhere on the board
LED-B03: U7.9 (IO0_5); also elsewhere on the board
LED-B04: U7.8 (IO0_4); also elsewhere on the board
LED-B05: U7.7 (IO0_3); also elsewhere on the board
LED-B06: U7.6 (IO0_2); also elsewhere on the board
LED-B07: U7.5 (IO0_1); also elsewhere on the board
LED-B08: U7.4 (IO0_0); also elsewhere on the board
LED-B09: U4.20 (IO1_7); also elsewhere on the board
LED-B10: U4.19 (IO1_6); also elsewhere on the board
LED-B11: U4.18 (IO1_5); also elsewhere on the board
LED-B12: U4.17 (IO1_4); also elsewhere on the board
LED-B13: U4.16 (IO1_3); also elsewhere on the board
LED-B14: U4.15 (IO1_2); also elsewhere on the board
LED-B15: U4.14 (IO1_1); also elsewhere on the board
LED-C01: U11.10 (IO0_6); also elsewhere on the board
LED-C02: U4.13 (IO1_0); also elsewhere on the board
LED-C03: U4.11 (IO0_7); also elsewhere on the board
LED-C04: U11.9 (IO0_5); also elsewhere on the board
LED-C05: U4.10 (IO0_6); also elsewhere on the board
LED-C06: U4.5 (IO0_1); also elsewhere on the board
LED-C07: U11.8 (IO0_4); also elsewhere on the board
LED-C08: U4.6 (IO0_2); also elsewhere on the board
LED-C09: U4.7 (IO0_3); also elsewhere on the board
LED-C10: U11.7 (IO0_3); also elsewhere on the board
LED-C11: U4.8 (IO0_4); also elsewhere on the board
LED-C12: U4.9 (IO0_5); also elsewhere on the board
LED-C13: U11.11 (IO0_7); also elsewhere on the board
LED-C15: U4.4 (IO0_0); also elsewhere on the board
LED-D01: U11.4 (IO0_0); also elsewhere on the board
LED-D02: U11.5 (IO0_1); also elsewhere on the board
LED-E01: U8.19 (IO1_6); also elsewhere on the board
LED-E02: U8.20 (IO1_7); also elsewhere on the board
Output-Res01: U7.17 (IO1_4); also elsewhere on the board
Output-Res02: U7.18 (IO1_5); also elsewhere on the board
Output-Res03: U7.19 (IO1_6); also elsewhere on the board
Output-Res04: U7.20 (IO1_7); also elsewhere on the board
Schluessel0: U10.18 (IO1_5); also elsewhere on the board
Schluessel1: U5.13 (IO1_0); also elsewhere on the board
Schluessel2: U10.16 (IO1_3); also elsewhere on the board
Schluessel3: U10.19 (IO1_6); also elsewhere on the board
VCC: C18.2, C19.2, C20.2, C21.2, C22.2, C23.2, C24.2, C25.2, C26.2, C27.2, U4.3 (A2), U4.24 (VDD), U5.3 (A2), U5.21 (A0), U5.24 (VDD), U6.2 (A1), U6.3 (A2), U6.24 (VDD), U7.2 (A1), U7.3 (A2), U7.21 (A0), U7.24 (VDD), U8.24 (VDD), U9.21 (A0), U9.24 (VDD), U10.2 (A1), U10.24 (VDD), U11.2 (A1), U11.21 (A0), U11.24 (VDD); also elsewhere on the board

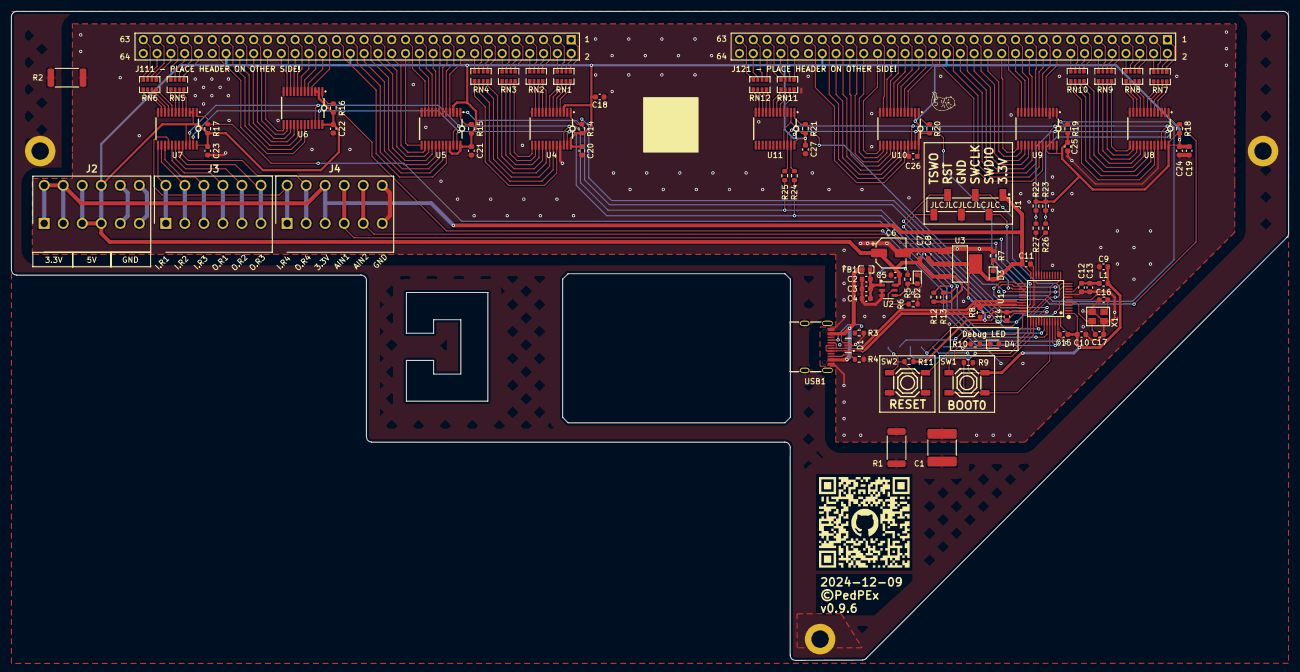
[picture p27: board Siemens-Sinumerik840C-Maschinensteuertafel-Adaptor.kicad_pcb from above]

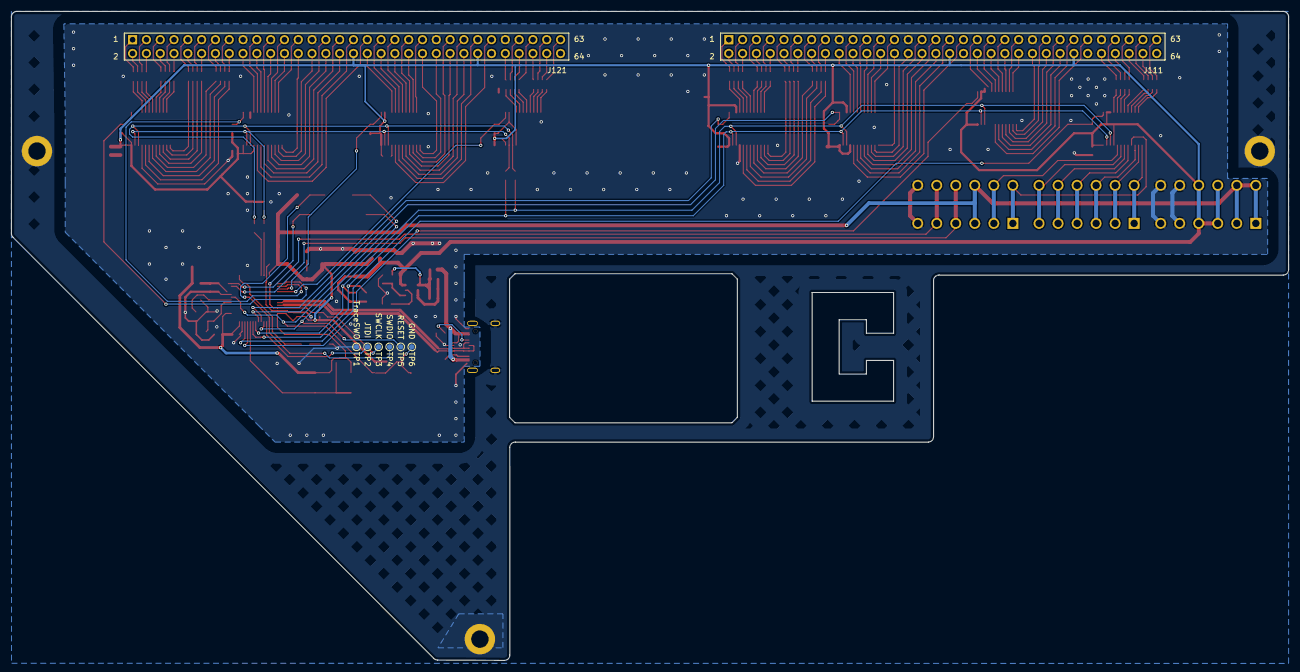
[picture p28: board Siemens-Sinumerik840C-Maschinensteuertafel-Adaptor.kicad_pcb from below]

Board: 2 copper layers, 235.0 x 119.4 mm, 102 parts (8 on the bottom side), 207 nets.

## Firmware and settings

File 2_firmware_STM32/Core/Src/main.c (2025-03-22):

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
/* Includes ------------------------------------------------------------------*/
#include "main.h"
#include "usb_device.h"

/* USER CODE BEGIN Includes */
#include "pca9555.h"
#include "pca9555.c"
#include <stdbool.h>
#include "usbd_cdc_if.h"
#include <stdio.h>
#include <string.h>

#define adc_used 1
#define number_of_exp 8
#define number_of_input_exp 5
#define timeout 10000 //10 seconds

/* USER CODE END Includes */

ADC_HandleTypeDef hadc;
DMA_HandleTypeDef hdma_adc;

I2C_HandleTypeDef hi2c1;
I2C_HandleTypeDef hi2c2;

TIM_HandleTypeDef htim3;

/* USER CODE BEGIN PV */

//Serial COM varaibles
uint8_t SerialConnected = 0;    //0=not connected; 1=connected; 2=connection lost
uint32_t LastTickConnected = 0; //HAL Tick variable - used for serial timeout detection
bool manual_CMD_Mode = 0;       //used for costum CMD "E1:0", in manual mode no timeout occurs

//array of expander IDs, get's initialised in the init_expanders function
PCA9555_HandleTypeDef exp[number_of_exp];
//variable for reading inputs when ISR was triggered
bool inputChanged = false;    //true = inputs will be read; false = no toggled input detected
uint16_t toggledGPIO = 0;      //toggled gpio pin (expander still needs to be determined)
//varaible to find out which inputs changed
uint16_t raw_exp_inputdata[number_of_input_exp];
//Encoder data
uint8_t enc_gray[2] = {0,0};
uint8_t enc_pos[2] = {0,0};
uint8_t enc_retval[2] = {0,0};

//ADC variables
uint16_t rawADCvalues[2];
uint16_t oldADCvalues[2];
uint16_t ADCvalues[2] = {0,0};
bool adc_convCompleted = 0;
uint8_t adc_hysteresis = 5;

//all input expanders with ID
uint8_t input_expander[number_of_input_exp] = {1,2,3,5,6};


/* USER CODE END PV */

void SystemClock_Config(void);
static void MX_GPIO_Init(void);
static void MX_DMA_Init(void);
static void MX_ADC_Init(void);
static void MX_I2C1_Init(void);
static void MX_I2C2_Init(void);
static void MX_TIM3_Init(void);
/* USER CODE BEGIN PFP */

uint8_t getinput(uint8_t expander, uint8_t pin);
void setOutput(uint8_t pin, uint8_t state);
void sendData(char sig, uint8_t pin, uint16_t state);
void USB_CDC_RxHandler(uint8_t* Buf, uint32_t Len);
void init_expanders();
void init_dataregs();
void serial_com_Handler();
void updateandsendEncoder(uint8_t pin, uint8_t pin_state);
void sendAllInputStatus();
uint8_t greyToBin(uint8_t n);


/* USER CODE END PFP */

/**
  * @brief  The application entry point.
  * @retval int
  */
int main(void)
{
  /* MCU Configuration--------------------------------------------------------*/

  /* Reset of all peripherals, Initializes the Flash interface and the Systick. */
  HAL_Init();

  /* Configure the system clock */
  SystemClock_Config();

  /* Initialize all configured peripherals */
  MX_GPIO_Init();
  MX_DMA_Init();
  MX_ADC_Init();
  MX_I2C1_Init();
  MX_I2C2_Init();
  MX_USB_DEVICE_Init();
  MX_TIM3_Init();
  /* USER CODE BEGIN 2 */
  HAL_StatusTypeDef HAL_status = 0, returnvalue = 0;

  init_expanders();
  init_dataregs();

  /* USER CODE END 2 */

  /* Infinite loop */
  /* USER CODE BEGIN WHILE */
  while (1)
  {
    /* USER CODE END WHILE */
    serial_com_Handler();
  }
}

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
/* USER CODE BEGIN 4 */

/**
  * @brief  Serial Handler for serial communication with LinuxCNC or for manual mode
  * @retval None
  */
void serial_com_Handler()
{
  //waiting for connection
  if(SerialConnected == 0)
  {
    //turn of DebugLED/Connection Status LED
    HAL_GPIO_WritePin(GPIOA, GPIO_PIN_3, false);
    //wait for connection
    while(SerialConnected == 0)
    {
      for(uint8_t i = 0; i <= 52 && SerialConnected == 0; i++)
      {
        if(i == 0)
        {
          setOutput(i, 1);
          setOutput(51, 0);
        }
        else if(i == 12 || i == 31 || i == 45 || i == 47)
        {
          setOutput(i-1, 0);
        }
        else if(i == 13 || i == 32 || i == 46 || i == 48)
        {
          setOutput(i, 1);
          setOutput(i-2, 0);
        }
        else if(i == 52)
        {
          init_ExpOutputs();
          break;
        }
        else
        {
          setOutput(i, 1);
          setOutput(i-1, 0);
        }

        CDC_Transmit_FS("E0:0\n", 5);
        HAL_Delay(200);  
      }
    }

  }

  //new ADC values?
  if(adc_convCompleted == 1)
  {
    ADCvalues[0] = (uint16_t)rawADCvalues[0] >> 2;
    ADCvalues[1] = (uint16_t)rawADCvalues[1] >> 2;
  
    //just send data in case something changed beyond the hysteresis
    if (abs((int)oldADCvalues[0] - (int)ADCvalues[0]) > adc_hysteresis && SerialConnected == 1)
    {
        sendData('A', 0, ADCvalues[0]);
        oldADCvalues[0] = ADCvalues[0];
    }
  
    if (abs((int)oldADCvalues[1] - (int)ADCvalues[1]) > adc_hysteresis && SerialConnected == 1)
    {
        sendData('A', 1, ADCvalues[1]);
        oldADCvalues[1] = ADCvalues[1];
    }
    
    adc_convCompleted = 0;
  }

  //stuff to do when connection is established
  if(SerialConnected == 1)
  {
    //timeout triggered? just checked in auto-mode (manual_CMD_Mode == 0)
    if(HAL_GetTick() - LastTickConnected > timeout && manual_CMD_Mode == 0 && LastTickConnected != 0)
    {
      CDC_Transmit_FS("F0:1\r\n", 6);
      //set connection status to connection lost
      SerialConnected = 2; 
      //reset all outputs
      init_ExpOutputs();
    }

    //input changed?
    if(inputChanged)
    {
      read_changed_Input(toggledGPIO);
    }
    //for more stuff
  }

  //if connection status is connection lost => blink LED 2x per second 
  while(SerialConnected == 2)
  {
    for(uint8_t k = 0; k <= 1 && SerialConnected == 2; k++)
    {
      for(uint8_t i = 0; i <= 51 && SerialConnected == 2; i++)
      {
        if(i == 12 || i == 31 || i == 45 || i == 47)
        {
          ;
        }
        else
        {
          setOutput(i, k);
        }
      }
      HAL_Delay(500);
      HAL_GPIO_TogglePin(GPIOA, GPIO_PIN_3);
    }
  }
}

/**
  * @brief  needs to be called when ISR for input change was detected
  * @retval None
  */
void read_changed_Input(uint16_t GPIO_Pin)
{
  //temp error variable
  HAL_StatusTypeDef HALreturn = 0;
  //find out which expander got input change
  uint8_t exp_interrupt = 255;  //init with error value
  uint8_t exp_data = 255;       //init with error value

  //Find out which expander initiated interrupt
  switch (GPIO_Pin)
  {
    /* case GPIO_PIN_4: //exp_int1 - no inputs
      exp_interrupt = 0; //expander 0
      exp_data = 255;
      break; */
    case GPIO_PIN_5: //exp_int2
      exp_interrupt = 1; //expander 1
      exp_data = 0;
      break;
    case GPIO_PIN_8: //exp_int3
      exp_interrupt = 2; //expander 2
      exp_data = 1;
      break;
    case GPIO_PIN_9: //exp_int4
      exp_interrupt = 3; //expander 3
      exp_data = 2;
      break;
    /* case GPIO_PIN_12: //exp_int5 - no inputs
      exp_interrupt = 4; //expander 4
      exp_data = 255;
      break; */
    case GPIO_PIN_13: //exp_int6
      exp_interrupt = 5; //expander 5
      exp_data = 3;
      break;
    case GPIO_PIN_14: //exp_int7
      exp_interrupt = 6; //expander 6
      exp_data = 4;
      break;
    /* case GPIO_PIN_15: //exp_int8 - no inputs
      exp_interrupt = 7; //expander 7
      exp_data = 255;
      break; */
    default:
      //return HAL_ERROR;
      Error_Handler();
      break;
  }

  //temp variable for storing read inputs and later calculating differences via bitwise XOR
  uint16_t temp_exp_inputs = 0;
  //reading inputdata from expander that initiated interrupt
  HALreturn = pca9555_readRegister(&exp[exp_interrupt], PCA9555_CB_INPUTS_PORTS, &temp_exp_inputs);
  //invert read value, bacause Siemens HMI uses Pull-Ups on all normal inputs and Pull-Downs on all "safety inputs"
  temp_exp_inputs = ~(temp_exp_inputs);

  //find out which inputs changed since last interrupt or initial input read
  temp_exp_inputs = temp_exp_inputs ^ raw_exp_inputdata[exp_data];
  //update value to detect changed pin(s) in the next interrupt event 
  raw_exp_inputdata[exp_data] = raw_exp_inputdata[exp_data] ^ temp_exp_inputs;

  //if serial communication is active
  if(SerialConnected == 1)
  {
    //test every bit of the 2 bytes for changed pin(s)
    for(uint8_t i = 0; i < 16; i++)
    {
      //detect a changed pin/bit - note: there could be the possibility, that mor than one input changed
      //hence all the handling needs to be done in the ISR and can not be done in the main function, a break from the for-loop is also not clever
      if((temp_exp_inputs >> i) & 0x0001)
      {
        //look up which input is connected to corresponding expander input pin
        uint8_t pressed_input = getinput(exp_interrupt, i);

        //change on encoder?
        if(pressed_input >= 64 && pressed_input <= 79)
        {
          //update encoder value(s)
          updateandsendEncoder(pressed_input, (raw_exp_inputdata[exp_data] >> i) & 0x0001);
          break;
        }
        else
        {
          //send state of individual pin via virtual serial port
          sendData('I', pressed_input, (raw_exp_inputdata[exp_data] >> i) & 0x0001);
        }
      }
    }
  }

  //Error handling
  if (HALreturn != HAL_OK || exp_data == 255 || exp_interrupt == 255)
  {
    Error_Handler();
  }

  //reset global flag
  inputChanged = false;
}

/**
  * @brief  init Data Registers state
  * @retval None
  */
void init_dataregs()
{
  //iterate over all input expanders
  for(uint8_t i = 0; i < number_of_input_exp; i++)
  {
    //read raw input data from every expander
    pca9555_readRegister(&exp[input_expander[i]], PCA9555_CB_INPUTS_PORTS, &raw_exp_inputdata[i]);
    //invert register
    raw_exp_inputdata[i] = ~(raw_exp_inputdata[i]);

    init_ExpOutputs();
  }
}

/**
  * @brief  Turn off all Expander outputs
  * @retval None
  */
void init_ExpOutputs()
{
  HAL_StatusTypeDef returnvalueinit = 0;

  for(uint8_t i = 0; i <= 15; i++)
  {
    //init EXP0
    returnvalueinit += pca9555_DigitalWrite(&exp[0], i, PCA9555_BIT_SET);
    //init EXP4
    returnvalueinit += pca9555_DigitalWrite(&exp[4], i, PCA9555_BIT_SET);
    //init EXP7
    returnvalueinit += pca9555_DigitalWrite(&exp[7], i, PCA9555_BIT_SET);
  }
  //init EXP3 - First Byte Outputs, Second Byte: 4 LSBits Outputs, 4 MSBits Inputs
  for(uint8_t i = 0; i <= 7; i++)
  {
    returnvalueinit += pca9555_DigitalWrite(&exp[3], i, PCA9555_BIT_SET);
  }
  for(uint8_t i = 12; i <= 15; i++)
  {
    returnvalueinit += pca9555_DigitalWrite(&exp[3], i, PCA9555_BIT_SET);
  }

  //Error handling
  if (returnvalueinit != HAL_OK)
  {
    Error_Handler();
  }
}

/**
  * @brief  Initialise all expanders
  * @retval None
  */
void init_expanders()
{
  //pause interrupts
  __disable_irq();
  //I2C start adress
  uint16_t address_expander = 0x20;
  //tmp value for error detection
  HAL_StatusTypeDef returnvalueinit = 0;
  
  //init Expanders on i2c busses - i know, the layout is "a bit weird" ...
  returnvalueinit += pca9555_init(&exp[4], &hi2c2, address_expander++);
  returnvalueinit += pca9555_init(&exp[5], &hi2c2, address_expander++);
  returnvalueinit += pca9555_init(&exp[6], &hi2c2, address_expander++);
  returnvalueinit += pca9555_init(&exp[7], &hi2c2, address_expander++);
  returnvalueinit += pca9555_init(&exp[0], &hi2c1, address_expander++);
  returnvalueinit += pca9555_init(&exp[1], &hi2c1, address_expander++);
  returnvalueinit += pca9555_init(&exp[2], &hi2c1, address_expander++);
  returnvalueinit += pca9555_init(&exp[3], &hi2c1, address_expander);

  //init Expanders used as Outputs (EXP0, EXP3, EXP4 and EXP7)
  //init EXP0
  for(uint8_t i = 0; i <= 15; i++)
  {
    returnvalueinit += pca9555_pinMode(&exp[0], i, PCA9555_PIN_OUTPUT_MODE, PCA9555_POLARITY_NORMAL);
  }
  //init EXP3 - First Byte Outputs, Second Byte: 4 LSBits Outputs, 4 MSBits Inputs
  for(uint8_t i = 0; i <= 7; i++)
  {
    returnvalueinit += pca9555_pinMode(&exp[3], i, PCA9555_PIN_OUTPUT_MODE, PCA9555_POLARITY_NORMAL);
  }
  for(uint8_t i = 12; i <= 15; i++)
  {
    returnvalueinit += pca9555_pinMode(&exp[3], i, PCA9555_PIN_OUTPUT_MODE, PCA9555_POLARITY_NORMAL);
  }
  //init EXP4
  for(uint8_t i = 0; i <= 15; i++)
  {
    returnvalueinit += pca9555_pinMode(&exp[4], i, PCA9555_PIN_OUTPUT_MODE, PCA9555_POLARITY_NORMAL);
  }
  //init EXP7
  for(uint8_t i = 0; i <= 15; i++)
  {
    returnvalueinit += pca9555_pinMode(&exp[7], i, PCA9555_PIN_OUTPUT_MODE, PCA9555_POLARITY_NORMAL);
  }

  init_ExpOutputs();

  /*
  //init Expanders used as Inputs (EXP1, EXP2, EXP3, EXP5 and EXP6)
  //init EXP1
  for(uint8_t i = 0; i <= 15; i++)
  {
    returnvalueinit += pca9555_pinMode(&exp[1], i, PCA9555_PIN_INPUT_MODE, PCA9555_POLARITY_INVERTED);
  }
  //init EXP2
  for(uint8_t i = 0; i <= 15; i++)
  {
    returnvalueinit += pca9555_pinMode(&exp[2], i, PCA9555_PIN_INPUT_MODE, PCA9555_POLARITY_INVERTED);
  }
  //init EXP3
  for(uint8_t i = 8; i <= 11; i++) //just 4 LSBits in second Byte are Inputs
  {
    returnvalueinit += pca9555_pinMode(&exp[3], i, PCA9555_PIN_INPUT_MODE, PCA9555_POLARITY_INVERTED);
  }
  //init EXP5
  for(uint8_t i = 0; i <= 15; i++)
  {
    returnvalueinit += pca9555_pinMode(&exp[5], i, PCA9555_PIN_INPUT_MODE, PCA9555_POLARITY_INVERTED);
  }
  //init EXP6
  for(uint8_t i = 0; i <= 15; i++)
  {
    returnvalueinit += pca9555_pinMode(&exp[6], i, PCA9555_PIN_INPUT_MODE, PCA9555_POLARITY_INVERTED);
  } */



  //reenable interrupts
  __enable_irq();

  //COMMENTED OUT because the command is working and setting all registers as intended but is not reporting correctly to HAL
  //Error handling
  /*if (returnvalueinit != HAL_OK)
  {
    Error_Handler();
  }*/
}

/**
  * @brief  ISR for the external interrupts
  * @retval None
  */
void HAL_GPIO_EXTI_Callback(uint16_t GPIO_Pin)
{
  //handling serial output of pressed input in function serial_com_Handler if "true" - nicer solution, but not reliable working
  if(false)
  {
    toggledGPIO = GPIO_Pin;
    inputChanged = true;
  }
  //handling serial output of pressed input within ISR if "false" - not a good solution, but only reliable working one
  else
  {
    //temp error variable
    HAL_StatusTypeDef HALreturn = 0;
    //find out which expander got input change
    uint8_t exp_interrupt = 255;  //init with error value
    uint8_t exp_data = 255;       //init with error value

    //Find out which expander initiated interrupt
    switch (GPIO_Pin)
    {
      /* case GPIO_PIN_4: //exp_int1 - no inputs
        exp_interrupt = 0; //expander 0
        exp_data = 255;
        break; */
      case GPIO_PIN_5: //exp_int2
        exp_interrupt = 1; //expander 1
        exp_data = 0;
        break;
      case GPIO_PIN_8: //exp_int3
        exp_interrupt = 2; //expander 2
        exp_data = 1;
        break;
      case GPIO_PIN_9: //exp_int4
        exp_interrupt = 3; //expander 3
        exp_data = 2;
        break;
      /* case GPIO_PIN_12: //exp_int5 - no inputs
        exp_interrupt = 4; //expander 4
        exp_data = 255;
        break; */
      case GPIO_PIN_13: //exp_int6
        exp_interrupt = 5; //expander 5
        exp_data = 3;
        break;
      case GPIO_PIN_14: //exp_int7
        exp_interrupt = 6; //expander 6
        exp_data = 4;
        break;
      /* case GPIO_PIN_15: //exp_int8 - no inputs
        exp_interrupt = 7; //expander 7
        exp_data = 255;
        break; */
      default:
        //return HAL_ERROR;
        Error_Handler();
        break;
    }

    //temp variable for storing read inputs and later calculating differences via bitwise XOR
    uint16_t temp_exp_inputs = 0;
    //reading inputdata from expander that initiated interrupt
    HALreturn = pca9555_readRegister(&exp[exp_interrupt], PCA9555_CB_INPUTS_PORTS, &temp_exp_inputs);
    //invert read value, bacause Siemens HMI uses Pull-Ups on all normal inputs and Pull-Downs on all "safety inputs"
    temp_exp_inputs = ~(temp_exp_inputs);
    
    //find out which inputs changed since last interrupt or initial input read
    temp_exp_inputs = temp_exp_inputs ^ raw_exp_inputdata[exp_data];
    //update value to detect changed pin(s) in the next interrupt event 
    raw_exp_inputdata[exp_data] = raw_exp_inputdata[exp_data] ^ temp_exp_inputs;

    //if serial communication is active
    if(SerialConnected == 1)
    {
      //test every bit of the 2 bytes for changed pin(s)
      for(uint8_t i = 0; i < 16; i++)
      {
        //detect a changed pin/bit - note: there could be the possibility, that mor than one input changed
        //hence all the handling needs to be done in the ISR and can not be done in the main function, a break from the for-loop is also not clever
        if((temp_exp_inputs >> i) & 0x0001)
        {
          //look up which input is connected to corresponding expander input pin
          uint8_t pressed_input = getinput(exp_interrupt, i);
    
          //change on encoder?
          if(pressed_input >= 64 && pressed_input <= 79)
          {
            //update encoder value(s)
            updateandsendEncoder(pressed_input, (raw_exp_inputdata[exp_data] >> i) & 0x0001);
            break;
          }
          else
          {
            //send state of individual pin via virtual serial port
            sendData('I', pressed_input, (raw_exp_inputdata[exp_data] >> i) & 0x0001);
          }
        }
      }
    }

    //Error handling
    if (/*HALreturn != HAL_OK || */ exp_data == 255 || exp_interrupt == 255)
    {
      Error_Handler();
    }
  }
}

/**
  * @brief  "ISR" for incoming serial msg
  * @retval None
  */
void USB_CDC_RxHandler(uint8_t* Buf, uint32_t Len)
{
  char CMD = 'a';                                             //variable for received command - see ArduinoConnector docs for mor info
  int pin = 0, state = 0;                                     //corresponding pin from Command, in the following example marked as 7: "O7:1"
  int i = sscanf((char*)Buf, "%c%d:%d", &CMD, &pin, &state);  //write received text to their corresponding variable
  
  //check for valid serial CMD
  if(CMD >= 'A' && CMD <= 'Z' && i == 3)
  {
    //serial connection command?
    if(CMD =='E')
    {
      if(SerialConnected != 1)
      {
        HAL_GPIO_WritePin(GPIOA, GPIO_PIN_3, true); //turn on LED
        SerialConnected = 1;                        //set serial status to connected 
        sendAllInputStatus();                     //send initial state
      }
      LastTickConnected = HAL_GetTick();  //write last Tick to tmp variable for timeout detection

      if(pin == 0)                        //machine mode
      {
        manual_CMD_Mode = 0;
      }
      else if(pin == 1)                   //manual mode
      {
        manual_CMD_Mode = 1;
      }
      else
      {
        //FAULT
        char sendBuf[15] = "Command fault!\n";
        CDC_Transmit_FS(sendBuf, strlen(sendBuf));
      }
    }
    //command to write output if connected
    else if(CMD == 'O' && SerialConnected == 1)
    {
      //set output to sent state
      setOutput(pin, state);
    }
    else if(CMD == 'A' && SerialConnected == 1)
    {
        //ADC needed?
        HAL_ADC_Start_DMA(&hadc, (uint32_t *)rawADCvalues, 2);
    }
    else
    {
      char sendBuf[20] = "command not found!\n";
      CDC_Transmit_FS(sendBuf, strlen(sendBuf));
    }
  }
  else
  {
    char sendBuf[16] = "fault detected!\n";
    CDC_Transmit_FS(sendBuf, strlen(sendBuf));
  }
}

/**
  * @brief  ISR for finished ADC conversion
  * @retval None
  */
void HAL_ADC_ConvCpltCallback(ADC_HandleTypeDef* hadc)
{
  adc_convCompleted = 1;
}

/**
  * @brief  send data via serial
  * @retval None
  */
void sendData(char sig, uint8_t pin, uint16_t state)
{
  //tmp variable to build message
  char sendBuf[12];
  //build message and write that to sendBuf
  sprintf(sendBuf, "%c%i:%i\r\n", sig, pin, state);
  //transmit message via serial
  uint8_t test = CDC_Transmit_FS(sendBuf, strlen(sendBuf));
  
  //HAL_Delay(100);
  //while (&hUsbDeviceFS.pClassData ->TxState != 0);

}

/**
  * @brief  setting output X? to state ? -> A15->1
  * @retval None
  */
void setOutput(uint8_t pin, uint8_t state)
{
  //LUT (LookUpTable)
  //8 bit value - 4 MSB = Expander 0...7; 4 LSB = 16 bit per Expander
  //expander 0: 0000|0000 up to 0000|1111; expander 1: 0001|0000 up to 0001|1111; ... expander 7: 0111|0000 up to 0111|1111; 
  static const uint8_t outputs[64] = {67, 75, 74, 66, 73, 68, 65, 69, 70, 64, 71, 72,255,114, 76, 77, //column A (expander 4 & 7)
                                      55, 54, 53, 52, 51, 50, 49, 48, 15, 14, 13, 12, 11, 10, 9, 255, //column B (expander 0 & 3)
                                      118,8,  7, 117, 6,  1, 116, 2,  3, 115, 4,  5, 119,255, 0, 255, //column C (expander 0 & 7)
                                      112,113,78,79,  60, 61, 62, 63,255,255,255,255,255,255,255,255};//column D, E, Res (expander 3, 4 & 7)
  
  
  //calculate expander from outputs-LUT (LUT = LookUpTable)
  //the 4 MSBs indicate which expander needs to be written to - identical to devide by 16 or right shift by 4 bits
  uint8_t expander_no = (outputs[pin] / 16);
  //calculate expander pin from outputs-LUT (LUT = LookUpTable)
  //the 4 LSBs indicate which expander needs to be written to - identical to modulo by 16 or by masking the 4 least segnificant bits
  uint8_t hw_pin = (outputs[pin])%16;

  //Error Handling
  if(expander_no > number_of_exp-1 || outputs[pin] == 255 || state < 0 || state > 1)
  {
    if(SerialConnected == 1 && manual_CMD_Mode == 0)
    {
      CDC_Transmit_FS("F1:1\n", 5);
      return;
    }
    if(SerialConnected == 1 && manual_CMD_Mode == 1)
    {
      CDC_Transmit_FS("F1:1\nOutput write Fault!\n",25);
      return;
    }
  }

  //write to calculated pin - state needs to be inverted
  pca9555_DigitalWrite(&exp[expander_no], hw_pin, 0b1 ^ state);
}
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

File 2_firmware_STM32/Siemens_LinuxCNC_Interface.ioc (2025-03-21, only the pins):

Mcu.UserName=STM32L151CCTx
PA1.Signal=ADC_IN1
PA11.Signal=USB_DM
PA12.Signal=USB_DP
PA13.Signal=SYS_JTMS-SWDIO
PA14.Signal=SYS_JTCK-SWCLK
PA15.Signal=SYS_JTDI
PA2.Signal=ADC_IN2
PA3.GPIO_Label=DebugLED
PA3.Signal=GPIO_Output
PB10.Signal=I2C2_SCL
PB11.Signal=I2C2_SDA
PB12.GPIO_Label=Exp_Int5
PB12.Signal=GPXTI12
PB13.GPIO_Label=Exp_Int6
PB13.Signal=GPXTI13
PB14.GPIO_Label=Exp_Int7
PB14.Signal=GPXTI14
PB15.GPIO_Label=Exp_Int8
PB15.Signal=GPXTI15
PB3.Signal=SYS_JTDO-TRACESWO
PB4.GPIO_Label=Exp_Int1
PB4.Signal=GPXTI4
PB5.GPIO_Label=Exp_Int2
PB5.Signal=GPXTI5
PB6.Signal=I2C1_SCL
PB7.Signal=I2C1_SDA
PB8.GPIO_Label=Exp_Int3
PB8.Signal=GPXTI8
PB9.GPIO_Label=Exp_Int4
PB9.Signal=GPXTI9
PH0-OSC_IN.Signal=RCC_OSC_IN
PH1-OSC_OUT.Signal=RCC_OSC_OUT

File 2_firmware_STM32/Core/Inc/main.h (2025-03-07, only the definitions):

#define DebugLED_Pin GPIO_PIN_3
#define DebugLED_GPIO_Port GPIOA
#define Exp_Int5_Pin GPIO_PIN_12
#define Exp_Int5_GPIO_Port GPIOB
#define Exp_Int5_EXTI_IRQn EXTI15_10_IRQn
#define Exp_Int6_Pin GPIO_PIN_13
#define Exp_Int6_GPIO_Port GPIOB
#define Exp_Int6_EXTI_IRQn EXTI15_10_IRQn
#define Exp_Int7_Pin GPIO_PIN_14
#define Exp_Int7_GPIO_Port GPIOB
#define Exp_Int7_EXTI_IRQn EXTI15_10_IRQn
#define Exp_Int8_Pin GPIO_PIN_15
#define Exp_Int8_GPIO_Port GPIOB
#define Exp_Int8_EXTI_IRQn EXTI15_10_IRQn
#define Exp_Int1_Pin GPIO_PIN_4
#define Exp_Int1_GPIO_Port GPIOB
#define Exp_Int1_EXTI_IRQn EXTI4_IRQn
#define Exp_Int2_Pin GPIO_PIN_5
#define Exp_Int2_GPIO_Port GPIOB
#define Exp_Int2_EXTI_IRQn EXTI9_5_IRQn
#define Exp_Int3_Pin GPIO_PIN_8
#define Exp_Int3_GPIO_Port GPIOB
#define Exp_Int3_EXTI_IRQn EXTI9_5_IRQn
#define Exp_Int4_Pin GPIO_PIN_9
#define Exp_Int4_GPIO_Port GPIOB
#define Exp_Int4_EXTI_IRQn EXTI9_5_IRQn

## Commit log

2024-09-02 finished most of schematic, init STM32 program
    [Extender-IO.kicad_sch, Headers.kicad_sch, Siemens-Sinumerik840C-Maschinensteuertafel-Adaptor.kicad_pcb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]
2024-09-05 finished schematics and board
    [Extender-IO.kicad_sch, Headers.kicad_sch, Siemens-Sinumerik840C-Maschinensteuertafel-Adaptor.kicad_pcb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]
2024-09-07 changed from STM32F103C8 over to STM32L151C8 changed controller pinout, minor tweaks in board design, added labels and debug pads
    [Extender-IO.kicad_sch, Headers.kicad_sch, Siemens-Sinumerik840C-Maschinensteuertafel-Adaptor.kicad_pcb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]
2024-10-18 finished v0.9.2
    [Extender-IO.kicad_sch, Headers.kicad_sch, Siemens-Sinumerik840C-Maschinensteuertafel-Adaptor.kicad_pcb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]
2024-10-18 pcb v0.9.3 finished
    [Extender-IO.kicad_sch, Headers.kicad_sch, Siemens-Sinumerik840C-Maschinensteuertafel-Adaptor.kicad_pcb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]
2024-10-25 PCB v0.9.4 - finished final prototype STM32 project reinitialised (F103C8 -> L151C8)
    [1824460000.stp, CRYSTAL-SMD_4P-L3.2-W2.5-BL_SIT8008BI.step, Extender-IO.kicad_sch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]
2024-10-27 PCB v0.9.5 - finished final prototype STM32 project pinout corrected
    [Extender-IO.kicad_sch, Headers.kicad_sch, Siemens-Sinumerik840C-Maschinensteuertafel-Adaptor.kicad_pcb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]
2025-03-06 started with PCB v0.9.6, software WIP communication with expander working, able to read inputs and set outputs, matrix for properly key-mapping and serial still needs to be done bugs from first badge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
    [Extender-IO.kicad_sch, Headers.kicad_sch, Siemens-Sinumerik840C-Maschinensteuertafel-Adaptor.kicad_pcb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]
2025-03-15 encoder working, problems with sending init state The encoders return their values, position as well as printed value on interface. Found a limitation in the STM32 USB_CDC HAL library, the controler 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
    [Siemens_LinuxCNC_Interface.ioc, main.c]

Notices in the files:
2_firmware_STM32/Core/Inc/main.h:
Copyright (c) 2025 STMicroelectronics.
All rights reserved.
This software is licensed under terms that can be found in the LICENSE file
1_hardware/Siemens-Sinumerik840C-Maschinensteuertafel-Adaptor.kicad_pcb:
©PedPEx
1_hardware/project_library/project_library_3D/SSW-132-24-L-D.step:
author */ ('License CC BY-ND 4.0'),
